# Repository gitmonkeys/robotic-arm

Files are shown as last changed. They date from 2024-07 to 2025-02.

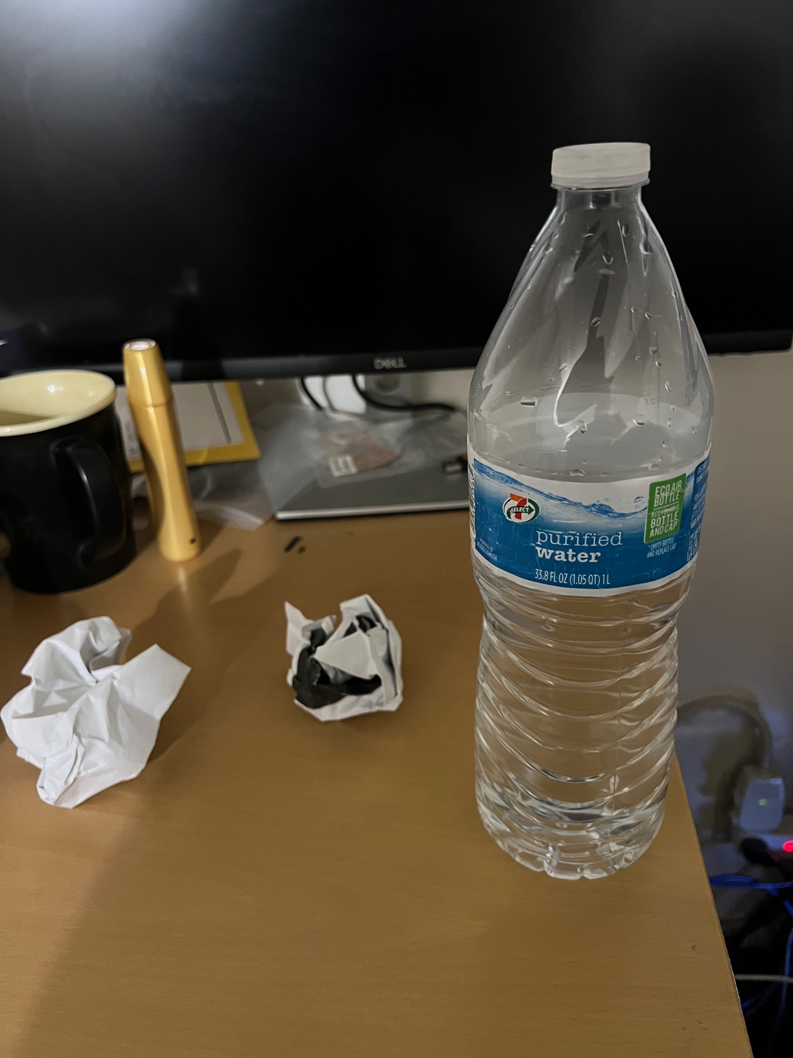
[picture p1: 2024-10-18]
training/object_detection/images/test/IMG_0963.jpeg

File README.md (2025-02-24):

# Autonomous Robotic Arm with 3 Degrees of Freedom Using Machine Learning and Object Detection

**Overview**

This project involves designing and building an autonomous robotic arm with three degrees of freedom (3DOF) that uses machine learning (ML) and object detection for intelligent decision-making. The robotic arm can autonomously identify, track, and interact with objects in its workspace. The inspiration for this project comes from Dum-E, the robotic assistant in the Iron Man movie. Our group wants to build an arm that could compete with industrial automation in price and efficiency. 

**Requirements**

* **Hardware**

1. Motors:
   * 2x Nema 23 Closed Loop Stepper Motor 3Nm for the base and shoulder joint. [Link](https://www.omc-stepperonline.com/nema-23-closed-loop-stepper-motor-3nm-425oz-in-with-magnetic-encoder-1000ppr-4000cpr-23hs45-4204-me1k)   
    * 1x Nema 23 Closed Loop Stepper Motor 1.85Nm for elbow joint. [Link](https://www.omc-stepperonline.com/nema-23-closed-loop-stepper-motor-1-85nm-256-9oz-in-with-magnetic-encoder-1000ppr-4000cpr-23hs30-2804-me1k)

2. Gearboxes:
   * 2x Nema 23 Stepper Motor EG Series Planetary Gearbox Gear Ratio 50:1. [Link](https://www.omc-stepperonline.com/eg-series-planetary-gearbox-gear-ratio-50-1-backlash-20-arc-min-for-10mm-shaft-nema-23-stepper-motor-eg23-g50-d10)
    * 1x 30:1 Worm Gearbox NMRV30. [Link](https://www.omc-stepperonline.com/30-1-worm-gearbox-nmrv30-worm-gear-speed-reducer-11mm-input-shaft-diameter-nmrv30-g30-d11)

3. Drivers:
   * 4x Closed Loop Stepper Driver V4.1 0-8.0A 24-48VDC. [Link](https://www.omc-stepperonline.com/closed-loop-stepper-driver-v4-1-0-8-0a-24-48vdc-for-nema-17-23-24-stepper-motor-cl57t-v41)

4. Microcontroller:
   * Raspberry Pi 4 Model B 4GB DDR4 RAM. [Link](https://www.microcenter.com/product/637834/raspberry-pi-4-model-b)
  
5. Power Supply:
   * 2x 400W 48V 8.30A 115/230V Switching Power Supply Stepper Motor. [Link](https://www.omc-stepperonline.com/400w-48v-8-3a-115-230v-switching-power-supply-stepper-motor-cnc-router-kits-s-400-48)

6. Camera Module:
   * Logitech - C270 720P Webcam. [Link](https://www.bestbuy.com/site/logitech-c270-720-webcam-with-noise-reducing-mics-black/9928354.p?skuId=9928354)

* **Software**

  * Object Detection Framework: Tensorflow Lite with MobilenetSSD
  * Libraries: pigpiod, openCV, numPy

**Related Link** : [Presentation](https://drive.google.com/file/d/11MK3jkFFWJjc2J69ZWIUt4JH5KeWML4S/view?usp=sharing)  [Video](https://drive.google.com/file/d/14PpU2gKORRkf9S9HrM6rWyZ0WrCm3C_z/view?usp=sharing)  [Video Demo](https://drive.google.com/file/d/12h4q9IPbSu7JaG7YCd0QZ_vuEIj181gn/view?usp=sharing)

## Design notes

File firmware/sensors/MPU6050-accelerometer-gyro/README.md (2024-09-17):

This directory contains appropriate python validation for testing quality and accuracy of sensor.

This directory includes:
* the code.py file, for testing the sensors
* the lib/ folder and all of its contents (including subfolders and .mpy or .py files)
* any assets (such as images, sounds, etc.)

Here's the Raspberry Pi wired with I2C, below is an image diagram:
* Pi 3V to sensor VCC (red wire)
* Pi GND to sensor GND (black wire)
* Pi SCL to sensor SCL (yellow wire)
* Pi SDA to sensor SDA (blue wire)

Wiring Diagram

You must use the appropriate CircuitPython9 on your microcontroller. For Raspberry Pi 4, simply run the following command on your Raspberry Pi's terminal
```
pip3 install adafruit-circuitpython-mpu6050 --break-system-packages
```
Disclaimer:
* Please note, in order to instal the mentioned drivers on our Raspberry Pi, we had to utilize ```--break-system-packages``` in order to get the driver to install due to a ```python3-pip``` limitation on Raspberry Pi. Feel free to remove the mentioned line and see if it works; otherwise, proceed with caution and install at your own risk.
* We recommend using a fresh Raspberry Pi for aformentioned drivers, with sole usecase being dedicated to DUM-E and not repurposed for other taks.

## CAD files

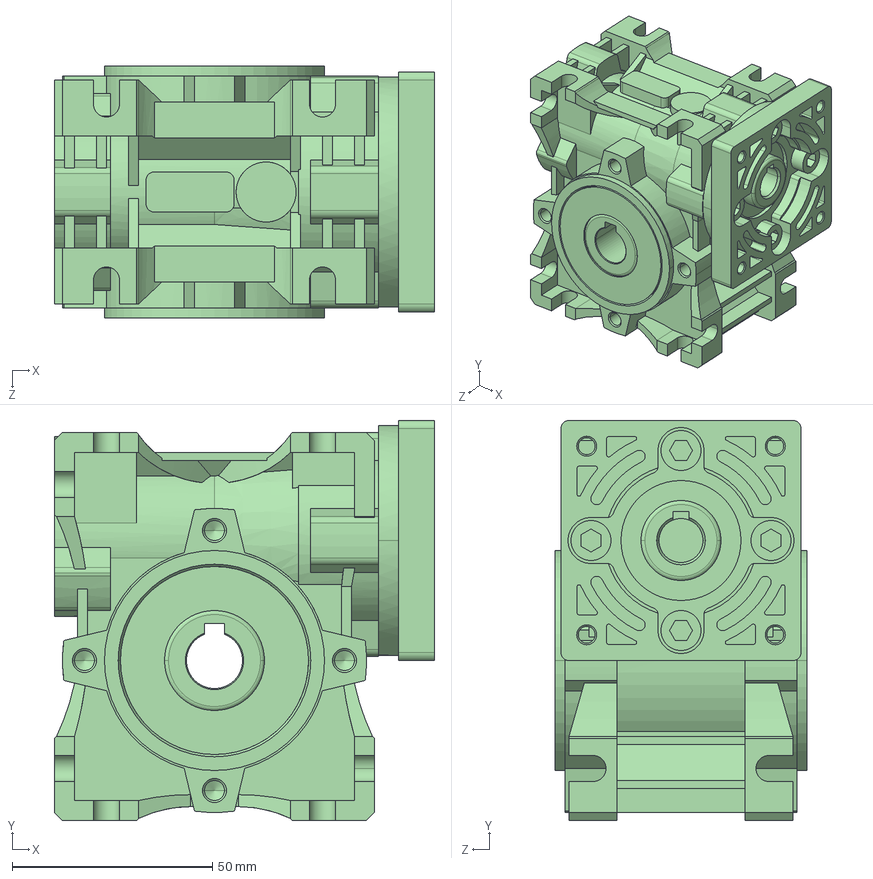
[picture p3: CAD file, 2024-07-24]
mechanics/gearbox-50-worm.STEP
95.0 x 100.0 x 63.0 mm

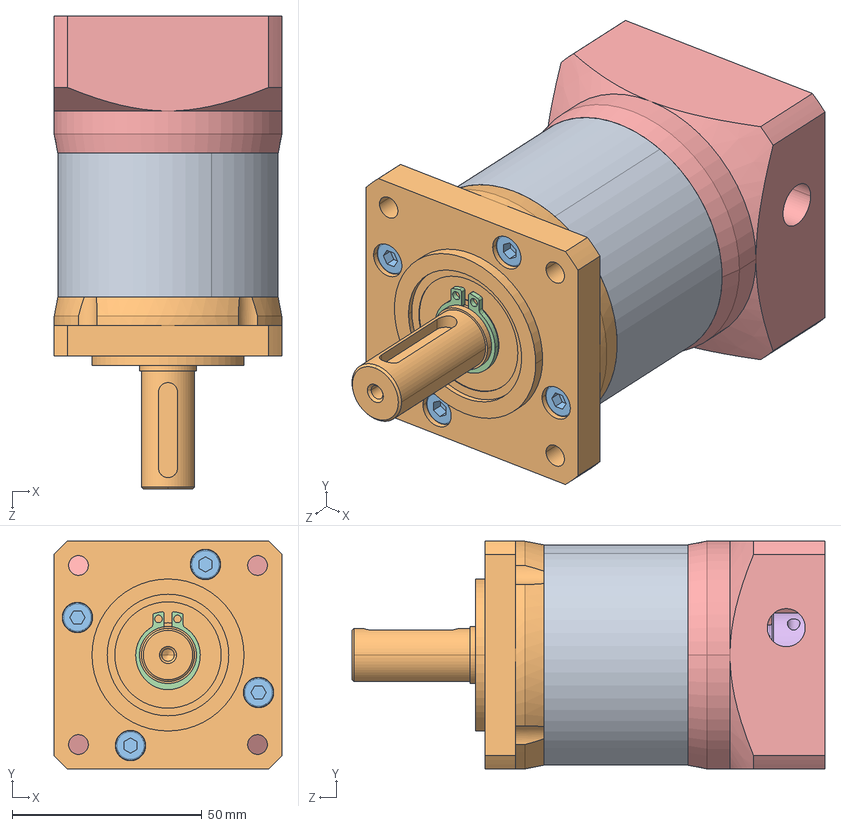
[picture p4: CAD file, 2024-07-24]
mechanics/gearbox-20.STEP
60.0 x 60.0 x 124.5 mm
60 gear ring-2
EG23 output shaft
M4hexagon socket head cap screw x 10
15circlip
EG23input flangeMB
EG23input shaft-10

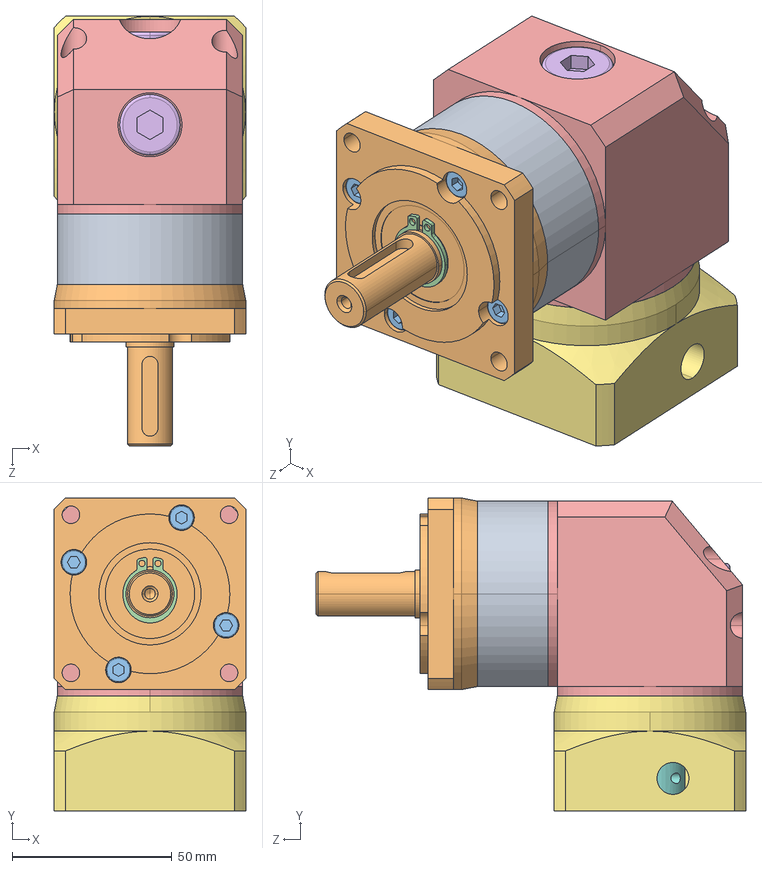
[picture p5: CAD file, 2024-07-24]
mechanics/right-gearbox-10.STEP
60.0 x 98.0 x 134.5 mm
60gear ring1
RYG23Output flange
M4hexagon socket head cap screw - ectype x 14
15outside capllipers
60Corner box
Head screw M12 x 2
RYG23Input flange MB
servo60 input axis -22

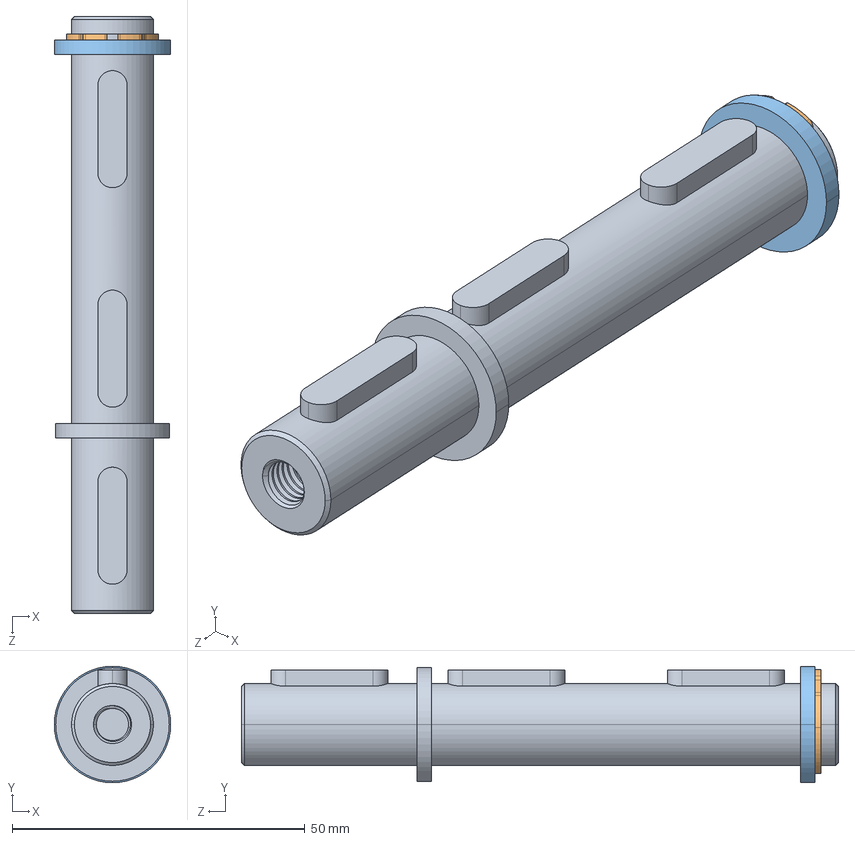
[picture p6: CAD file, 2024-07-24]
mechanics/extended-shaft.STEP
19.9 x 19.9 x 102.0 mm
RV30-SHAFT-AS
RV30-CIRCLIP
RV30-PLAIN WASHER

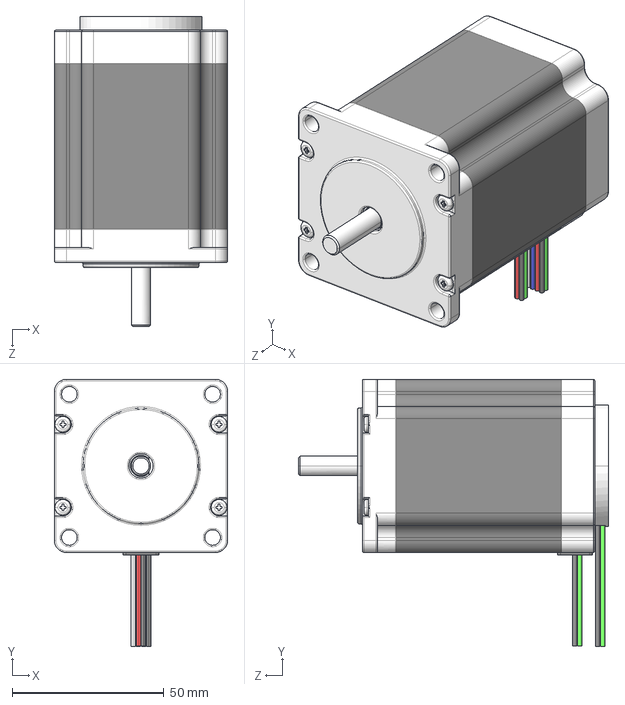
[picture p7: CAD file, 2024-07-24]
mechanics/motor-1.8.STEP
57.0 x 88.0 x 102.0 mm

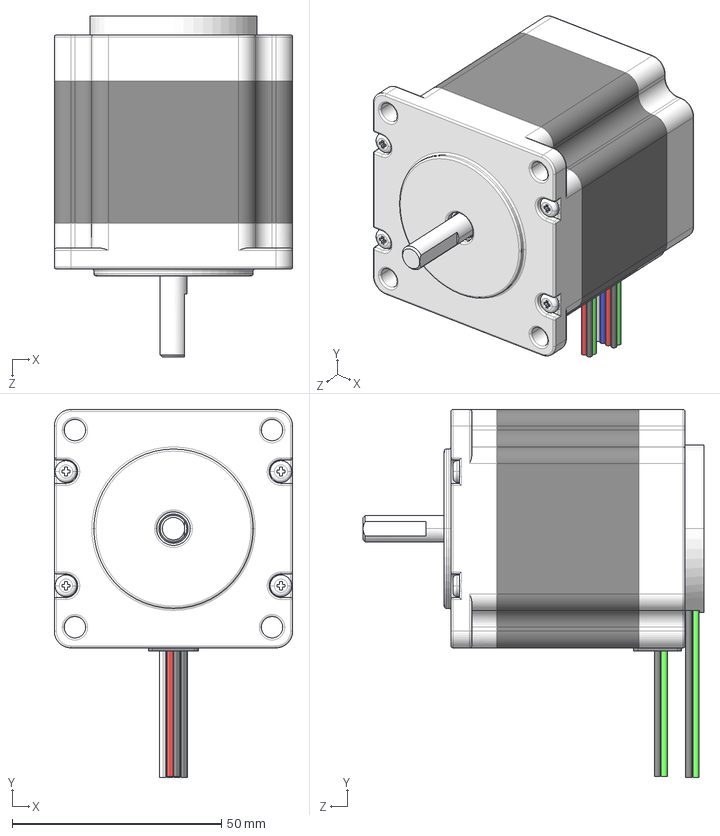
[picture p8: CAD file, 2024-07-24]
mechanics/motor-1.2.STEP
57.0 x 88.0 x 81.5 mm

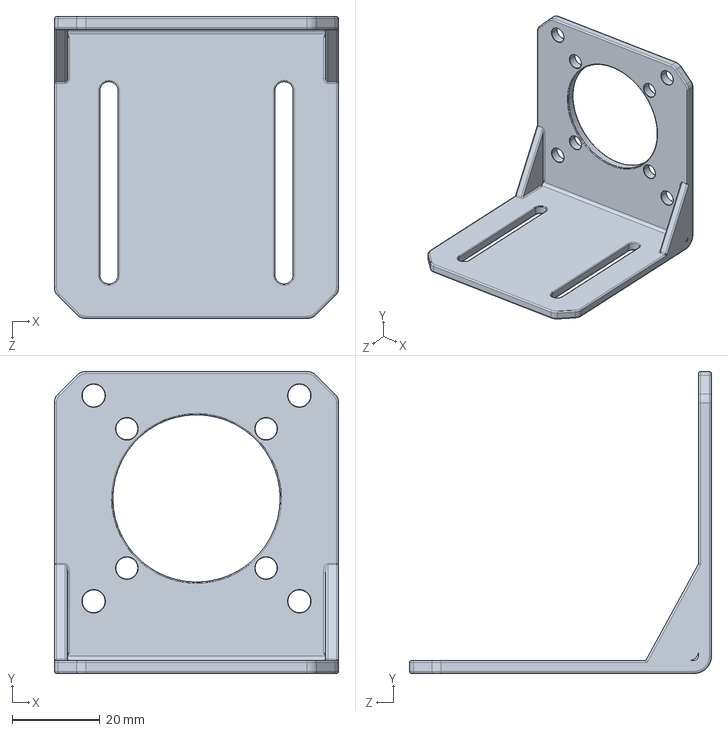
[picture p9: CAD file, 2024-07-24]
mechanics/l-bracket.STEP
65.0 x 69.0 x 69.0 mm

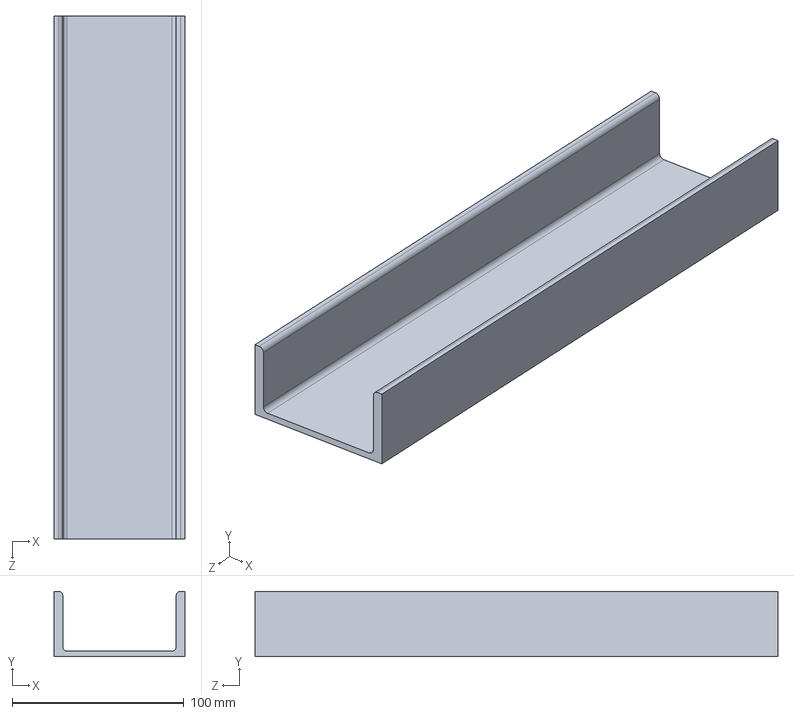
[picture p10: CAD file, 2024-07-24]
mechanics/u-Channel.STEP
76.2 x 38.1 x 304.8 mm

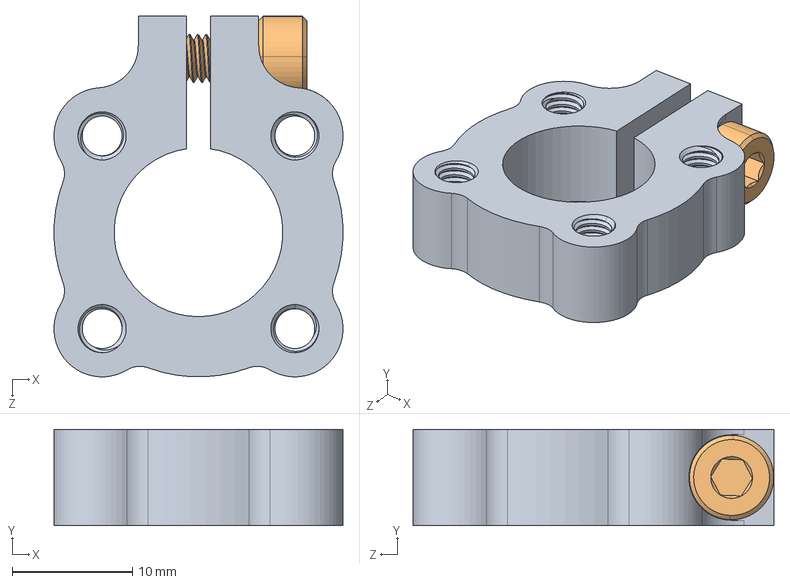
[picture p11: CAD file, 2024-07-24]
mechanics/motor-shaft-clamp.STEP
24.0 x 8.00 x 29.9 mm
2800-0004-0010_90128A207

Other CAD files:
mechanics/gearbox-50.STEP

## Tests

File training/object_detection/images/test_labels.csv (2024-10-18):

filename | width | height | class | xmin | ymin | xmax | ymax
IMG_0963.jpeg | 3024 | 4032 | trash paper | 4 | 2327 | 759 | 3156
IMG_0963.jpeg | 3024 | 4032 | trash paper | 1039 | 2227 | 1610 | 2823
IMG_0963.jpeg | 3024 | 4032 | trash bottle | 1768 | 475 | 2756 | 3385

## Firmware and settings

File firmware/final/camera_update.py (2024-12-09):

import cv2
import numpy as np
from PIL import Image
import time

# Global list to store the scanned object centers and their classes
scanned_object_centers = []

# Function to create a homogeneous transformation matrix
def homogeneous_transform():
    T = np.array([[1, 0, 0, -24],  # X-axis translation 
                  [0, -1, 0, 59],  # Y-axis translation (upside down)
                  [0, 0, -1, 0],   # Z-axis remains unchanged
                  [0, 0, 0, 1]])   # Homogeneous coordinates
    return T

# Function to apply the transformation matrix to a point
def apply_transformation(T, point):
    point_homogeneous = np.array([point[0], point[1], point[2], 1])  # Convert point to homogeneous coordinates
    transformed_point_homogeneous = np.dot(T, point_homogeneous)     # Apply the transformation matrix
    return transformed_point_homogeneous[:3]                         # Return transformed 3D point

# Function to preprocess the image
def preprocess_image(image, target_size=(320, 320)):
    img = Image.fromarray(image)
    img.thumbnail(target_size, Image.LANCZOS)
    new_img = Image.new("RGB", target_size, (0, 0, 0))  # Padding with black
    paste_position = (
        (target_size[0] - img.size[0]) // 2,
        (target_size[1] - img.size[1]) // 2
    )
    new_img.paste(img, paste_position)
    img_array = np.array(new_img).astype(np.uint8)
    img_array = np.expand_dims(img_array, axis=0)
    return img_array

pred_recycle = 0.75
pred_trash = 0.65
# Updated function for class detection
def class_detection(image):
    """
    Perform object classification using a TensorFlow Lite model.
    """
    import tflite_runtime.interpreter as tflite

    model_path = '/home/jroc/Desktop/final/model.tflite'
    interpreter = tflite.Interpreter(model_path=model_path)
    interpreter.allocate_tensors()

    input_details = interpreter.get_input_details()
    output_details = interpreter.get_output_details()

    img_array = preprocess_image(image)
    input_index = input_details[0]['index']
    interpreter.set_tensor(input_index, img_array)
    interpreter.invoke()
    output_data = interpreter.get_tensor(output_details[0]['index'])

    prediction_probability = np.max(output_data)
    predicted_class_index = np.argmax(output_data)

    # Custom classification logic
    if prediction_probability >= pred_recycle:
        predicted_class = 'recycle'
    elif pred_trash < prediction_probability < pred_recycle:
        predicted_class = 'trash'
    else:
        predicted_class = None  # Skip this object

    return predicted_class, prediction_probability

# Function to capture an image, detect objects, and store their centers
def get_sorted_object_coordinates():
    global scanned_object_centers

    cap = cv2.VideoCapture(0)
    cap.set(cv2.CAP_PROP_FRAME_WIDTH, 1280)  # Set the width of the frame
    cap.set(cv2.CAP_PROP_FRAME_HEIGHT, 720)  # Set the height of the frame

    if not cap.isOpened():
        print("Error: Unable to open the camera.")
        return None

    actual_width = cap.get(cv2.CAP_PROP_FRAME_WIDTH)
    cm_to_pixel = 54 / actual_width  # Conversion factor from pixels to centimeters

    T = homogeneous_transform()
    scanned_object_centers.clear()

    ret, frame = cap.read()
    if not ret:
        print("Error: Cannot capture frame from the camera.")
        cap.release()
        return None

    gray_image = cv2.cvtColor(frame, cv2.COLOR_BGR2GRAY)

    # Convert to binary image using adaptive thresholding
    binary_image = cv2.adaptiveThreshold(
        gray_image, 255,
        cv2.ADAPTIVE_THRESH_GAUSSIAN_C,
        cv2.THRESH_BINARY_INV, 11, 2
    )

    # Find contours in the binary image
    contours, _ = cv2.findContours(binary_image, cv2.RETR_EXTERNAL, cv2.CHAIN_APPROX_SIMPLE)

    scanned_object_centers.clear()

    for contour in contours:
        # Filter out small contours to avoid noise
        if cv2.contourArea(contour) < 1000:
            continue

        x, y, w, h = cv2.boundingRect(contour)

        # Ignore objects that are too small or too large
        if w * cm_to_pixel < 1 or h * cm_to_pixel < 1 or w * cm_to_pixel > 8 or h * cm_to_pixel >15:
            continue

        object_roi = frame[y:y+h, x:x+w]
        object_class, probability = class_detection(object_roi)

        # Skip objects not meeting thresholds
        if object_class is None:
            continue

        # Calculate the center of the bounding box
        X_Location = (x + w / 2) * cm_to_pixel  # X coordinate in cm
        Y_Location = (y + h / 2) * cm_to_pixel  # Y coordinate in cm
        Z_Location = 0  # Z-location assumed to be 0 for 2D

        # Apply the transformation matrix to the detected location
        transformed_point = apply_transformation(T, (X_Location, Y_Location, Z_Location))

        # Append the transformed object center to the list
        scanned_object_centers.append((transformed_point[0], transformed_point[1], object_class))

        # Draw the bounding box and center on the original image
        cv2.rectangle(frame, (x, y), (x + w, y + h), (0, 255, 0), 2)  # Draw bounding box

        # Prepare text for object class and probability
        label = f"{object_class} ({probability:.2f})"
        label_position = (x, y - 10 if y - 10 > 10 else y + 10)
        cv2.putText(frame, label, label_position, cv2.FONT_HERSHEY_SIMPLEX, 0.5, (255, 0, 0), 2)

        # Draw center point
        center = (int(transformed_point[0] / cm_to_pixel), int(transformed_point[1] / cm_to_pixel))
        cv2.circle(frame, center, 5, (0, 0, 255), -1)  # Draw center point

    # Sort the scanned object centers by their distance from the origin (0, 0)
    scanned_object_centers.sort(key=lambda obj: np.sqrt(obj[0]**2 + obj[1]**2))
    
    # Release the camera
    cap.release()
    
    # Return the image with drawn objects
    return frame

# Main function
def main():
    print("Starting program...")
    while True:
        # Detect and process objects
        image_with_objects = get_sorted_object_coordinates()

        if image_with_objects is None:
            print("Exiting due to no image...")
            break

        # Print the coordinates of detected objects
        print("\nScanned Object Coordinates and Classes:")
        for i, obj in enumerate(scanned_object_centers):
            print(f"Object {i + 1}: X={obj[0]:.2f} cm, Y={obj[1]:.2f} cm, Class={obj[2]}")

        # Display the image
        cv2.imshow("Detected Objects", image_with_objects)

        # Wait for a key press (ESC to exit)
        if cv2.waitKey(1) & 0xFF == 27:  # ESC key
            print("Exiting program on user request.")
            break

    cv2.destroyAllWindows()

if __name__ == "__main__":
    main()

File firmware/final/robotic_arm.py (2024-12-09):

import motor_control
import kinematics
import cv2
import camera_update
import time

def main():
    # Initialize the robot's starting positions
    motor_control.initialize_position()
   

    processed_objects = []  # List to track already processed objects

    while True:
        user_input = input("Press 'c' to continue setting up the robot arm: ")
        if user_input.lower() == 'c':
            break
        else:
            print("Please press 'c' to continue.")

    while True:
        # Call get_stored_object_coordinates from camera_update.py
        image_with_objects = camera_update.get_sorted_object_coordinates()
        
        cv2.imshow("Detected Objects", image_with_objects)
        time.sleep(0.2)
        
        if image_with_objects is None or len(camera_update.scanned_object_centers) == 0:
            print("No objects detected. Waiting...")

            # Continue waiting if no objects are detected
            if cv2.waitKey(1) & 0xFF == 27:  # ESC key to exit
                print("Exiting the program.")
                break
            continue
        

        print("\nScanned Object Coordinates:")

        new_objects = []
        for obj in camera_update.scanned_object_centers:
            # Check if the object has already been processed within a small tolerance
            if not any(
                abs(obj[0] - p[0]) < 0.5 and abs(obj[1] - p[1]) < 0.5
                for p in processed_objects
            ):
                new_objects.append(obj)

        for i, obj in enumerate(new_objects):
            print(f"Object {i + 1}: X={obj[0]:.2f} cm, Y={obj[1]:.2f} cm")

            z = 1  # Default z-coordinate
            if kinematics.is_within_workspace(obj[0], obj[1], z):
                theta1, theta2, theta3 = kinematics.inverse_kinematics(obj[0], obj[1], z)
                print(f"\nCalculated joint angles:")
                print(f"Theta1 = {theta1:.2f} degrees")
                print(f"Theta2 = {theta2:.2f} degrees")
                print(f"Theta3 = {theta3:.2f} degrees")

                motor_control.go_target(theta1, theta2, theta3)

                if obj[2] == 'trash':
                    motor_control.go_trash(theta1, theta2, theta3)
                else:
                    motor_control.go_recycle(theta1, theta2, theta3)

                time.sleep(0.2)  # Delay to avoid rapid repeated movements

                # Add processed object to the list
                #processed_objects.append(obj)

        #cv2.imshow("Detected Objects", image_with_objects)

        k = cv2.waitKey(5)  # Wait for a key press
        if k == 27:  # ESC key to exit
            break
    camera_update.canned_object_centers.clear()
    cv2.destroyAllWindows()  # Clean up the window
    motor_control.clear_gpio()  # Disconnect from pigpio

if __name__ == "__main__":
    main()

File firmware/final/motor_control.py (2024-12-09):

#motro_control.py
import pigpio
import time


#SERVO_GPIO = 18  # Servo for the third joint
GRIPPER_SERVO_GPIO = 19  # Servo for the gripper

# GPIO pins for first stepper
PUL_PIN_1 = 23
DIR_PIN_1 = 24
ENA_PIN_1 = 25
gear_ratio1 = 50 # =4.5

# GPIO pins for second stepper
PUL_PIN_2 = 22
DIR_PIN_2 = 27
ENA_PIN_2 = 17
gear_ratio2 = 50

# GPIO pins for third stepper
#examples
PUL_PIN_3 = 5
DIR_PIN_3 = 6
ENA_PIN_3 = 26
gear_ratio3 = 30

# Constants
delay = 0.0001
microsteps_per_revolution = 800  # Microsteps per full revolution


gripper_position = 0

# Initialize pigpio
pi = pigpio.pi()  # Connect to pigpio daemon
if not pi.connected:
    exit()

def initialize_position():
    """
    Set initial positions: open the gripper and set the main servo motor to 90 degrees.
    """
    
    
    global gripper_position
    gripper_position = 0
    open_gripper()          # Open the gripper
    
    pi.write(ENA_PIN_1, 1)  # Turn on stepper motor 1
    pi.write(ENA_PIN_2, 1)  # Turn on stepper motor 2
    pi.write(ENA_PIN_3, 1)  # Turn ontepper motor 3
    
def clear_gpio():
    pi.set_servo_pulsewidth(GRIPPER_SERVO_GPIO, 0)  # Turn off the gripper servo
    pi.write(ENA_PIN_1, 0)  # Turn off stepper motor 1
    pi.write(ENA_PIN_2, 0)  # Turn off stepper motor 2
    pi.write(ENA_PIN_3,0)
    pi.stop()  # Disconnect from pigpio
  
def move_servo_smoothly(target_position, step_duration):
    # Initial position for gripper
    global gripper_position
    pi.set_servo_pulsewidth(GRIPPER_SERVO_GPIO, int(500 + (gripper_position / 270.0 )* 2000))  # 
    
    while gripper_position != target_position:
        if gripper_position < target_position:
            gripper_position += 1  # Increase angle
        else:
            gripper_position -= 1  # Decrease angle
        
        pulse_width = int(500 + (gripper_position / 270.0) * 2000)
        pi.set_servo_pulsewidth(GRIPPER_SERVO_GPIO, pulse_width)
        
        time.sleep(step_duration)  # delay

def move_gripper(position):
    pulse_width = int(500 + (position / 270.0) * 2000)
    pi.set_servo_pulsewidth(GRIPPER_SERVO_GPIO, pulse_width)

def open_gripper():
    move_servo_smoothly(135,0.01)

def close_gripper():
    move_servo_smoothly(0,0.01)

def degrees_to_microsteps(degrees, gear_ratio):
    return int((degrees / 360.0) * microsteps_per_revolution * gear_ratio)


def step_motor(pul_pin, dir_pin, microsteps, delay):
    pi.write(dir_pin, 1 if microsteps > 0 else 0)
    for _ in range(abs(microsteps)):
        pi.write(pul_pin, 1)
        time.sleep(delay)
        pi.write(pul_pin, 0)
        time.sleep(delay)


# Moving to target
def go_target(theta1, theta2, theta3):
    print("Moving to target...")
    
    # Move first arm
    microsteps1 = degrees_to_microsteps(theta1, gear_ratio1)
    step_motor(PUL_PIN_1, DIR_PIN_1, microsteps1, delay)
    
    # Move third arm
    microsteps3=degrees_to_microsteps(theta3, gear_ratio3)
    step_motor(PUL_PIN_3, DIR_PIN_3, microsteps3,delay)
    
    # Move second arm
    microsteps2 = degrees_to_microsteps(theta2, gear_ratio2)
    step_motor(PUL_PIN_2, DIR_PIN_2, microsteps2, delay)
    
    print("Pick up the object")
    # Close gripper
    close_gripper()
    time.sleep(0.2)
# Moving to trash and then go home

def go_trash(theta1, theta2, theta3):
    print("Moving to trash and returning home...")

    # Move second arm up to 45 degrees
    adjusted_theta2 = -theta2 - 45
    microsteps2 = degrees_to_microsteps(adjusted_theta2, gear_ratio2)
    step_motor(PUL_PIN_2, DIR_PIN_2, microsteps2, delay)

    # Move first arm, go to trash
    adjusted_theta1 = -theta1 - 15
    microsteps1 = degrees_to_microsteps(adjusted_theta1, gear_ratio1)
    step_motor(PUL_PIN_1, DIR_PIN_1, microsteps1, delay)
    
    print("Drop off the object")
    # Open gripper
    open_gripper()
    time.sleep(0.2)
    
    print("returning to home")
    # Return arms to initial position
    microsteps1_back = degrees_to_microsteps(15,gear_ratio1)
    step_motor(PUL_PIN_1, DIR_PIN_1, microsteps1_back, delay)

    microsteps2_back = degrees_to_microsteps(45, gear_ratio2)
    step_motor(PUL_PIN_2, DIR_PIN_2, microsteps2_back, delay)
    
    microsteps3 =degrees_to_microsteps(-theta3, gear_ratio3)
    step_motor(PUL_PIN_3, DIR_PIN_3, microsteps3,delay)
    
    time.sleep(0.5)
 # Moving to recycle and then go home   

def go_recycle(theta1, theta2, theta3):
    print("Moving to recycle and returning home...")

    # Move second arm up to 45 degrees
    adjusted_theta2 = -theta2 -45
    microsteps2 = degrees_to_microsteps(adjusted_theta2, gear_ratio2)
    step_motor(PUL_PIN_2, DIR_PIN_2, microsteps2, delay)

    # Move first arm, go to trash
    adjusted_theta1 = 180 -theta1 
    microsteps1 = degrees_to_microsteps(adjusted_theta1, gear_ratio1)
    step_motor(PUL_PIN_1, DIR_PIN_1, microsteps1, delay)
    
    print("Drop off the object")
    # Open gripper
    open_gripper()
    time.sleep(0.2)
    
    print("returning to home")
    # Return arms to initial position
    microsteps1_back = degrees_to_microsteps(-180,gear_ratio1)
    step_motor(PUL_PIN_1, DIR_PIN_1, microsteps1_back, delay)

    microsteps2_back = degrees_to_microsteps(45, gear_ratio2)
    step_motor(PUL_PIN_2, DIR_PIN_2, microsteps2_back, delay)
    
    microsteps3 =degrees_to_microsteps(-theta3, gear_ratio3)
    step_motor(PUL_PIN_3, DIR_PIN_3, microsteps3,delay)
    
    time.sleep(0.5)
"""
try:
    initialize_position()
    while True:
        user_input = input("Enter angles (theta1, theta2, theta3) (or 'q' to quit): ")
        if user_input.lower() == 'q':
            break
        theta1, theta2, theta3 = map(float, user_input.split(','))  # Split string into list
        
        # Move first arm
        microsteps1 = degrees_to_microsteps(theta1, gear_ratio1)
        step_motor(PUL_PIN_1, DIR_PIN_1, microsteps1, delay)
        time.sleep(0.5)
    
        # Move second arm
        microsteps2 = degrees_to_microsteps(theta2, gear_ratio2)
        step_motor(PUL_PIN_2, DIR_PIN_2, microsteps2, delay)
        time.sleep(0.5)
                # Move second arm
        microsteps3 = degrees_to_microsteps(theta3, gear_ratio3)
        step_motor(PUL_PIN_3, DIR_PIN_3, microsteps3, delay)
        time.sleep(0.5)
        # test servo motor
        #close the gripper
        close_gripper()
        time.sleep(1)
        open_gripper()
        time.sleep(1)
        close_gripper()
 	
finally:
	clear_gpio()

"""

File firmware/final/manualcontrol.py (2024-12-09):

import RPi.GPIO as GPIO
import time
import curses  # To capture key presses

# Define GPIO pins
PUL_PIN = 22  #
DIR_PIN = 27  # Direction pin
ENA_PIN = 17  # Optional enable
SERVO_PIN = 19  # servo PWM control pin

# Motor parameters
STEP_DELAY = 0.0001  # Delay between steps
STEPS_PER_REV = 800
STEPS_PER_DEGREE = STEPS_PER_REV / 360

# Define step counts
step = int(5 * STEPS_PER_DEGREE)

# servo
SERVO_MIN_DUTY = 2.5  # Duty cycle for 0 degrees
SERVO_MAX_DUTY = 12.5  # Duty cycle for 180 degree

# Setup GPIO mode
GPIO.setmode(GPIO.BCM)
GPIO.setup(PUL_PIN, GPIO.OUT)
GPIO.setup(DIR_PIN, GPIO.OUT)
GPIO.setup(ENA_PIN, GPIO.OUT)
GPIO.setup(SERVO_PIN, GPIO.OUT)

# Setup PWM for the servo motor (50Hz is typical for servos)
servo_pwm = GPIO.PWM(SERVO_PIN, 50)
servo_pwm.start(0)  # Initialize with 0 duty cycle (servo off)


def set_servo_angle(angle):
    duty_cycle = SERVO_MIN_DUTY + (angle / 180) * (SERVO_MAX_DUTY - SERVO_MIN_DUTY)
    servo_pwm.ChangeDutyCycle(duty_cycle)
    time.sleep(2)  # Give some time for the servo to move
    GPIO.output(SERVO_PIN, GPIO.LOW)


# Function to rotate the motor
def rotate_motor(steps, direction):
    GPIO.output(DIR_PIN, direction)  # Set direction
    GPIO.output(ENA_PIN, GPIO.HIGH)  # Enable the driver

    for _ in range(steps):
        GPIO.output(PUL_PIN, GPIO.HIGH)
        time.sleep(STEP_DELAY)
        GPIO.output(PUL_PIN, GPIO.LOW)
        time.sleep(STEP_DELAY)
    # End for
    GPIO.output(ENA_PIN, GPIO.LOW)  # Disable the driver


# Function to step the motor once
def step_motor(direction):
    GPIO.output(DIR_PIN, direction)  # Set direction
    GPIO.output(ENA_PIN, GPIO.HIGH)  # Enable the driver

    # Pulse to make one step
    GPIO.output(PUL_PIN, GPIO.HIGH)
    time.sleep(STEP_DELAY)
    GPIO.output(PUL_PIN, GPIO.LOW)
    time.sleep(STEP_DELAY)


def main(stdscr):
    # Clear screen and set up
    stdscr.clear()
    curses.cbreak()
    stdscr.keypad(True)

    try:
        while True:
            key = stdscr.getch()

            if key == ord('r'):
                # Step right (one step at a time)
                # print("Stepping right...")
                rotate_motor(step, GPIO.HIGH)
            elif key == ord('l'):
                # Step left (one step at a time)
                # rint("Stepping left...")
                rotate_motor(step, GPIO.LOW)

            elif key == ord('q'):
                # Stop the motor
                print("Stopping...")
                GPIO.output(ENA_PIN, GPIO.LOW)
                break
            if key == ord('c'):
                set_servo_angle(180)  # Close the gripper (move to 180 degrees)
            elif key == ord('o'):
                set_servo_angle(0)  # Open the gripper (move to 0 degrees)


    except KeyboardInterrupt:
        print("Program interrupted")

    finally:
        print("Cleaning up GPIO...")
        GPIO.cleanup()


# Initialize curses wrapper
curses.wrapper(main)

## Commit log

2024-09-07 added code for motor control
2024-09-16 Validation firmware for sensors added. Please visit "sensors" directory. Follow instructions per README files.
2024-09-16 validations provided for sensors were condenced.
2024-09-17 control 2 motors
2024-09-27 double check result with foward kinematic
2024-09-27 organized code
    [assembly.FCStd, extended-shaft.FCStd, extended-shaft.STEP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]
2024-09-27 added inverse kinematic
2024-10-11 added gearboxes config for each motor
2024-10-18 added object detection training compatible with RPiOS
    [test_labels.csv, train_labels.csv]
